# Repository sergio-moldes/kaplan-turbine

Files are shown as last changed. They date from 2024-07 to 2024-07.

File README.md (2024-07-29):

# Kaplan Turbine Design

## Project Description

This project involves the design and analysis of a Kaplan-type turbine, which includes the sizing and analysis of the necessary parameters for the design of the runner, distributor, draft tube, and spiral casing. A CAD design has been created, and CFD simulations have been carried out to verify the performance of the design.

## Technologies Used

- **3D Modeling**: SolidWorks
- **Technical Documentation**: AutoCAD

## Repository Contents

- `/cad_models`: Contains CAD files in .stl, .step, .iges formats.
- `/documentation`: Technical drawings and project documentation in PDF format.

## Installation and Usage

To view and modify the CAD models:

1. Clone the repository: `git clone https://github.com/sergio-moldes/turbina-kaplan.git`
2. Open the files in SolidWorks or your preferred software.

## Contributions

Contributions are welcome. Please open an issue or submit a pull request to discuss any changes you wish to make.

## License

This project is licensed under the MIT License - see the [LICENSE](LICENSE) file for details.

## Project Documentation

The project has been thoroughly documented in the following PDF file: [Kaplan Turbine Design Documentation](documentation/Memoria_turbina_kaplan_final.pdf)

### Documentation Summary

#### 1. Introduction

Describes the project objective and provides an overview of the Kaplan turbine design.

#### 2. Nomenclature and Symbols

List of symbols and nomenclature used in the design calculations.

#### 3. Runner Calculations

Detailed calculations for the sizing of the runner, including initial parameters, outer diameter, free passage section, and hydraulic performance.

#### 4. Distributor Design

Calculations and design of the distributor blades, incidence angle, and blade height.

#### 5. Draft Tube Calculations

Cavitation analysis and suction height, sizing of the draft tube.

#### 6. Spiral Casing Design

Sizing and design of the spiral casing that directs the flow to the runner.

#### 7. CAD Design

CAD design process of the runner, distributor, draft tube, and spiral casing, including chord and angle correction.

### Project Images

Here are some images of the final CAD design:

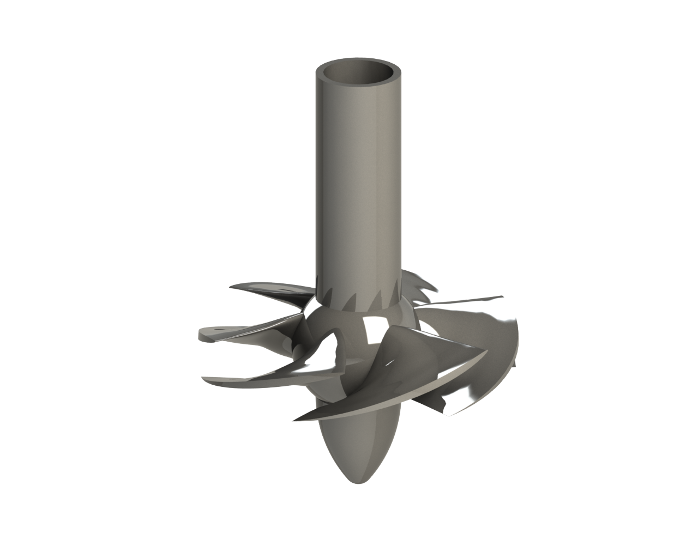
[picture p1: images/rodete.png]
Runner

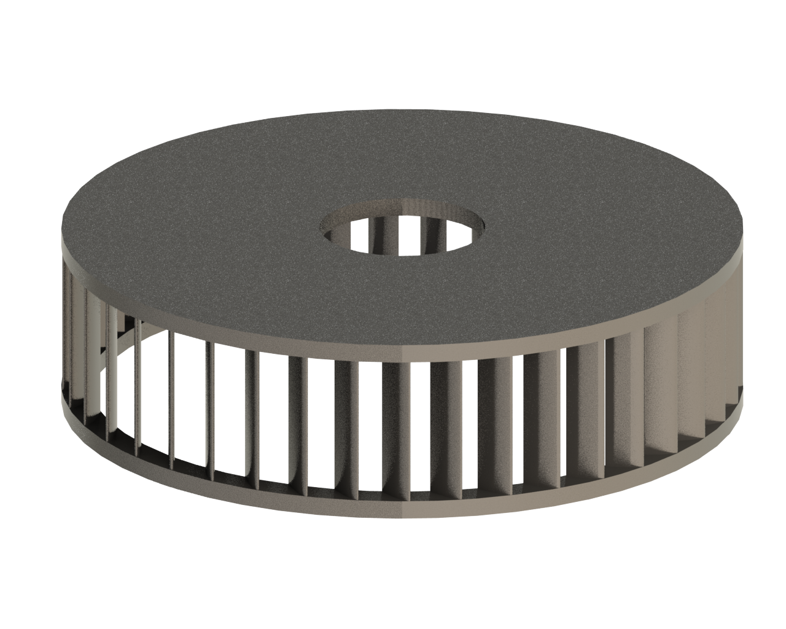
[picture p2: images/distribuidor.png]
Distributor

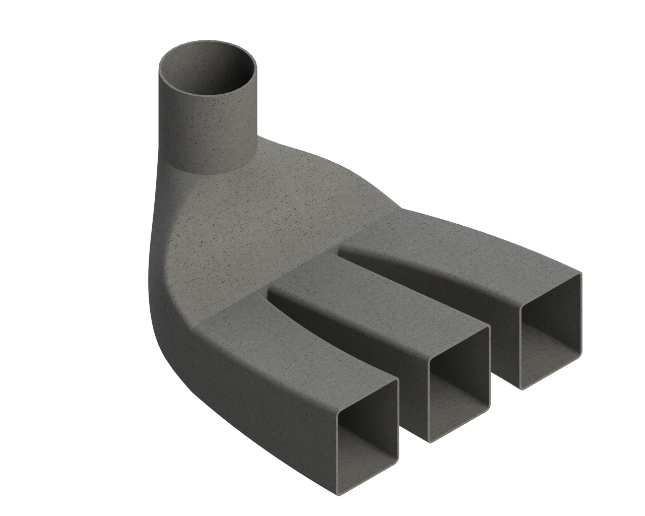
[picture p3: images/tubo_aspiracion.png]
Draft Tube

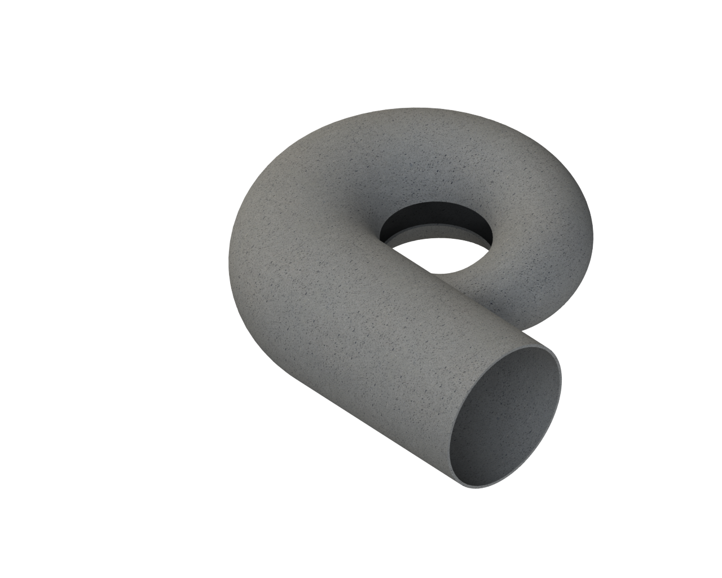
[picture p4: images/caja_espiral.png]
Spiral Casing


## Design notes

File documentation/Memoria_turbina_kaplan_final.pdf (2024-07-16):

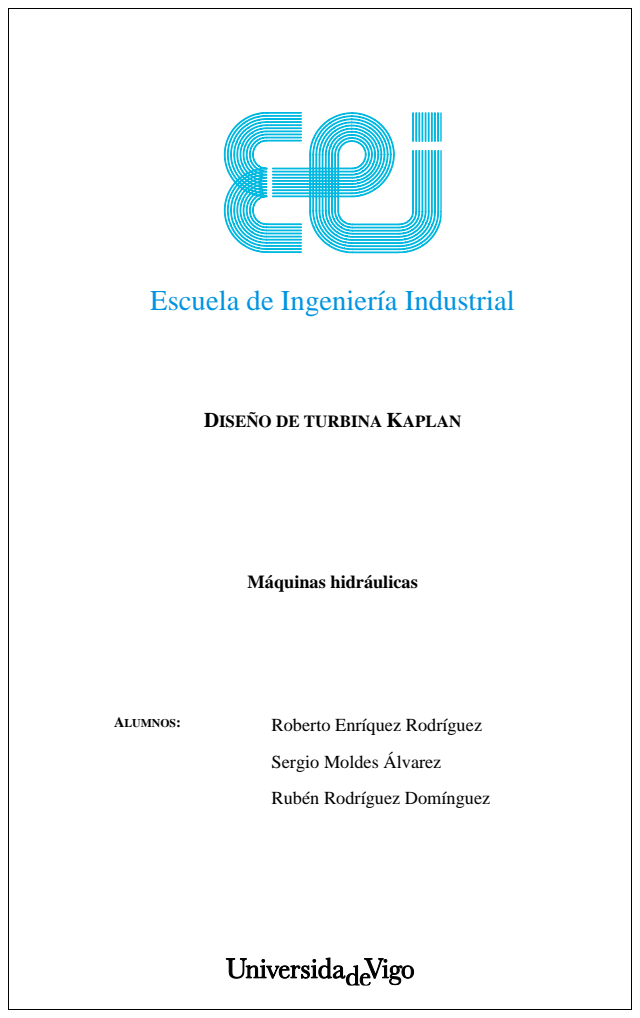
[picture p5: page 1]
Máquinas hidráulicas; ALUMNOS:; Roberto Enríquez Rodríguez

Escuela de Ingeniería Industrial

DISEÑO DE TURBINA KAPLAN

Sergio Moldes Álvarez

Rubén Rodríguez Domínguez

DISEÑO DE TURBINA KAPLAN¡ERROR! NO SE ENCUENTRA EL ORIGEN DE LA REFERENCIA.

CONTENIDO

ÍNDICE DE TABLAS

ÍNDICE DE FIGURAS

### 1 INTRODUCCIÓN

En este documento se realiza el diseño previo al diseño fino de una turbina tipo Kaplan. Estas, son turbinas axiales, donde el flujo es paralelo al eje de rotación, y de reacción pura, donde el fluido cambia de presión a medida que se desplaza a través de la turbina, cediendo su energía. Emplean energía cinética y de presión para mover el rodete, donde antes de llegar el agua al rodete, parte de la energía de presión que trae el agua en su caída se transforma en energía cinética en el distribuidor.

El agua a la salida del rodete se dirige al tubo de aspiración, generándose una depresión, con el fin de aumentar la energía hidráulica absorbida por el rodete. Este tubo desemboca en el canal de desagüe, devolviendo el agua al cauce.

Este tipo de turbina opera con alturas pequeñas y caudales grandes, siendo clasificada como rápidas, teniendo un valor de velocidad específica superior a 300.

El punto de operación estudiado en este documento es de:

H = 36,2 (m) Q = 280 (

m³

s

)

Para ello se realiza el dimensionamiento y análisis de los parámetros necesarios para el diseño del rodete, distribuidor, caja espiral y tubo de aspiración, con el fin de cumplir el punto de operación mencionado anteriormente. Para ello se realizarán los cálculos, sus correspondientes comprobaciones, la elección del perfil a emplear en los álabes y posteriormente el diseño en CAD.

### 2 NOMENCLATURA Y SIMBOLOGÍA

RODETE
SÍMBOLO | NOMBRE | UNIDADES
ns | Velocidad específica | rpm
Q | Caudal | m³ /s
H | Altura de diseño de la turbina | m
N | Potencia útil | CV − MW
n | Velocidad de rotación | rpm
p | Pares de polos | -
f | Frecuencia | Hz
η | Rendimiento total | %
D1 | Diámetro exterior | m
d1 | Diámetro interior | m
Q11 | Engullimiento | m³ /s
u | Velocidad periférica o de arrastre | m/s
u1 | Velocidad periférica o de arrastre a la entrada del rodete | m/s
u2 | Velocidad periférica o de arrastre a la salida del rodete | m/s
g | Gravedad | m/s 2
S | Sección libre de paso | m²
ηH | Rendimiento hidráulico | %
Vm | Velocidad meridional | m/s
V1 | Velocidad absoluta a la entrada del rodete | m/s
V2 | Velocidad absoluta a la salida del rodete | m/s
Vu1 | Componente periférica de la velocidad absoluta a la entrada del rodete | m/s
Vu2 | Componente periférica de la velocidad absoluta a la salida del rodete | m/s
β1 | Ángulo de los álabes a la entrada del rodete | Grados
β2 | Ángulo de los álabes a la salida del rodete | Grados
β∞ | Ángulo de los álabes suponiendo álabes infinitos | Grados
W1 | Velocidad relativa a la entrada del rodete | m/s
W2 | Velocidad relativa a la salida del rodete | m/s
W∞ | Velocidad relativa suponiendo álabes infinitos | m/s
λ | Constante para el cálculo de la cuerda | -
l | Cuerda del perfil | m

t | Paso entre álabes | m
Cl | Coeficiente de sustentación | -
F | Fuerza soportada por las palas | N
P | Presión teórica | Pa
S | Superficie del álabe | m²

DISTRIBUIDOR
SÍMBOLO | NOMBRE | UNIDADES
Vm0 | Componente meridiana radial de la velocidad absoluta de salida | m/s
KVm0 | Factor multiplicativo de la componente meridiana radial | -
g | Gravedad | 2 m/s
H | Altura de diseño de la turbina | m
r | Radio externo del rotor | m
Vu1 | Componente periférica de la velocidad absoluta a la entrada del rodete para el radio externo del rotor | m/s
C | Constante | -
D0 | Diámetro máximo del rodete sobredimensionado | m
D1 | Diámetro máximo del rodete | m
Vu0 | Componente periférica de la velocidad absoluta en el distribuidor | m/s
V0 | Velocidad absoluta en el distribuidor | m/s
B0 | Altura de las directrices | m
α0 | Ángulo de incidencia | Grados

TUBO DE ASPIRACIÓN

SÍMBOLO | NOMBRE | UNIDADES
σ | Coeficiente de Thoma | -
ns | Velocidad específica | rpm
Hs | Altura de succión | m
Hb | Valor de la presión atmosférica local | m
H | Altura de diseño de la turbina | m
ℎv | Tensión del vapor de agua | m. c. a
D3 | Diámetro de entrada del tubo de aspiración | m
A | Altura del tubo hasta el rodete | m
L’ | Longitud entre eje de la turbina y salida del tubo, con ángulo | m

CAJA ESPIRAL
SÍMBOLO | NOMBRE | UNIDADES

Ve | Velocidad de entrada en la caja | m/s
g | Gravedad | 2 m/s
H | Altura de diseño | m
Correspondencia | Factor de caudal correspondiente a la sección estudiada | -
Q | Caudal de diseño | m³ /s
D | Diámetro de la sección de la caja espiral | m

### 3 DIAGRAMA DE FLUJO

### 4 CÁLCULOS DEL RODETE

### 4.1 Parámetros de inicio

Conocido el punto de operación, mencionado anteriormente, siendo una altura de H = 36,2 metros y un caudal de Q = 280 m³/s, inicialmente se busca obtener el valor de la velocidad específica (ns) a partir de la siguiente fórmula:

ns =

n ∗ √N
H ∗ √H

4

[4.1.1]

Para su cálculo se necesita el valor de la velocidad de rotación (n) y el valor de la potencia útil (N), los cuales se obtienen iterando.

Primero, para la obtención del valor de la potencia útil (N), se prefija un valor de rendimiento total, a través de la siguiente fórmula:

N =

1000 ∗ η ∗ Q ∗ H
75

[4.1.2]

Como primer valor se escoge un rendimiento total de η = 90 %, para el cual se obtiene una potencia de N = 121632 CV. Observando este valor, el rendimiento total podría encontrarse entre el 93-94 % según la siguiente tabla extraída de la guía, debido a que el valor de la potencia es superior a 50000 CV.

Tabla 1. Rendimiento frente a potencia.

Teniendo esto en cuenta, se recalculará el valor de la potencia con un rendimiento del 94 %, obteniéndose un valor de N = 127038 CV.
Para el cálculo de la velocidad de rotación (n) se prefija el valor de la velocidad específica empleada en la guía siendo de ns = 457 rpm y el valor de N calculado anteriormente, despejando:

n =

ns ∗ H

5/4
√N

[4.1.3]

Se obtiene un valor de n = 113,85 rpm, correspondiendo para dicha velocidad un par de polos de 26’35, que aproximando al valor entero resulta de 26. Se recalcula el valor de n para 26 pares de polos (p), siendo de 115,39 rpm. Esto es calculado a partir de la siguiente expresión y sabiendo que la frecuencia de trabajo es de f = 50 Hz:

p =

60 ∗ f
n

[4.1.4]

Ya obtenido los valores de la velocidad de rotación (n) y la potencia útil (N), a partir de la fórmula X, se obtiene un valor de ns = 463,158 rpm, próximo al valor prefijado de 457 rpm.

No obstante, se busca un valor de la velocidad específica incluso más próximo para el cual se emplea un η = 91,5 %, obteniendo ns = 456,957 rpm ≈ 457 rpm.

A modo de resumen, los valores obtenidos durante las iteraciones son:

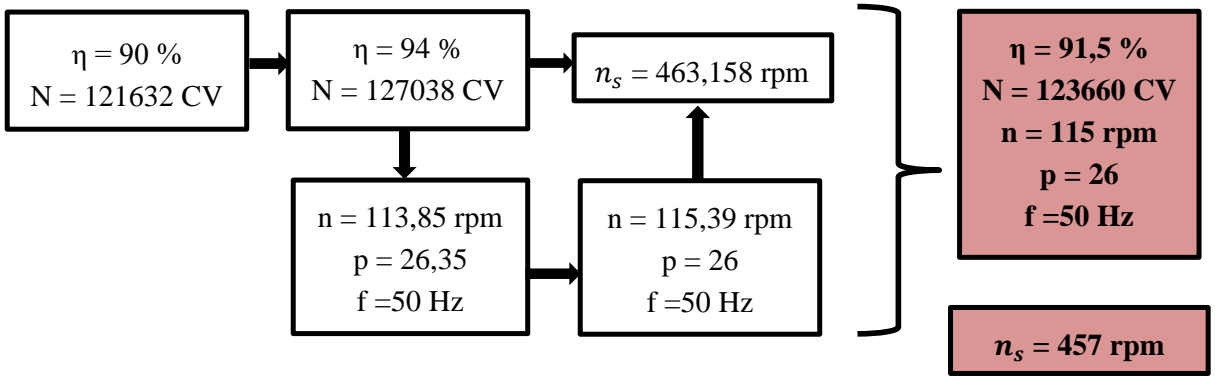
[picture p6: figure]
n = 113,85 rpm; n = 115,39 rpm; ns = 463,158 rpm; n = 115 rpm; ns = 457 rpm

Tras un proceso iterativo de comprobación de los resultados obtenidos en el los cálculos posteriores con respecto a los intervalos de valores correctos para el tipo de turbina a dimensionar, se decide emplear los siguientes parámetros para un mejor ajuste:

Los valores finales obtenidos, son destacados en color verde, siendo los parámetros de inicio que definen la turbina Kaplan (normal) en cuestión, obteniendo una potencia útil, expresada en megavatios de 94,23 MW.

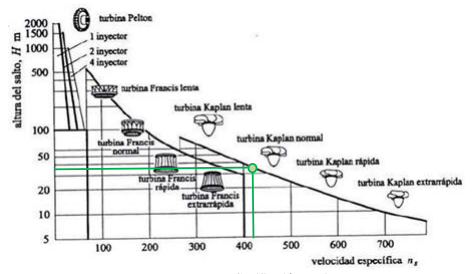
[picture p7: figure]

Figura 1. Clasificación turbinas.

η = 93,5 %
N = 126363 CV
n = 107 rpm
p = 28
f =50 Hz

ns = 429 rpm

### 4.2. Dimensionado del rodete

### 4.2.1. Diámetro exterior

Para la obtención del valor del diámetro externo del rodete, se valoran las 3 opciones expuestas por la guía siendo las siguientes:
- En primera instancia, se puede resolver a partir de la obtención de 2 diámetros, siendo los extremos del intervalo donde se encontrará el valor del diámetro, empleándose la siguiente fórmula:
D1 (m) = 4,8 a 5,5 ∗ √
Q
n

3
= (6, 615 ∼ 7, 579) m | [4.2.1]
- Otra opción planteada es su obtención a través del valor de engullimiento Q11, el cual es atribuido a la descarga consumida por una turbina semejante con valores unitarios de diámetro y altura.
A partir de la siguiente tabla y el valor de la velocidad específica ns = 457 rpm, se interpola para conseguir el valor del engullimiento.

Tabla 2. Engullimiento Q11.

Se obtiene un valor de Q11 = 1′356, con el cual ya se puede obtener el valor del diámetro, con la siguiente fórmula:

D1 = √
Q
Q11 ∗ √H

= √
280
1′356 ∗ √36′2
= 5, 857 m | [4.2.2]
- Como tercera posibilidad, el valor del diámetro (D1), se puede obtener a partir de u1s ,
conocida la velocidad específica, se accede a la siguiente tabla:

Tabla 3. U1s frente ns.

Interpolando se obtiene un valor de u1s = 1, 358, donde despejando el diámetro de la siguiente formula podemos obtener un resultado de:

u1s =

u1
√2 ∗ g ∗ H

=

π ∗ D1 ∗ n
60 ∗ √2 ∗ g ∗ ℎ

D1 =

u1s ∗ 60 ∗ √2 ∗ g ∗ ℎ
π ∗ n

= 7,680 m

[4.2.3]

A continuación, se resumen los valores de D1 obtenidos por los 3 métodos, donde finalmente se tomará como valor único y de referencia, la media de dichos resultados obtenidos:

Valores D1 (m)

D1(4,8) | 6,615
D1 (5,5) | 7,579
D1 (Q11) | 5,857
D1 (u1s) | 7,680
D1 (promedio) | 7,097

Tabla 4. Resumen valores D1.

### 4.2.2. Diámetro del cubo central

El diámetro del cubo central corresponde al diámetro interior, donde para su cálculo se realizará siguiendo 2 caminos con la finalidad de encontrar los mejores resultados. La guía propone realizar una aproximación, escogiendo un valor de entre el 40-50 % del diámetro exterior, no obstante, se considera realizar también una interpolación a través de la tabla 2 de este proyecto, siendo en función de la velocidad específica.

Inicialmente, se procede al cálculo del diámetro interior a través de la interpolación y la tabla mencionada, siendo el siguiente intervalo:

ns | d1/D1
400 | 0,450
429 | 0,444
500 | 0,430

Tabla 5. Cálculo d1.

Se obtiene que:

d1
D1

= 0

′444 → d1 = 3, 15 m | [4.2.4]

### 4.2.3. Sección libre de paso

Una vez determinados los valores del diámetro interior (d1) y exterior (D1) del rodete, se calcula la sección que atraviesa el fluido en su paso por él, obteniéndose un valor de:

S =

(D1

2 − d1

2
) ∗ π
4
= 31, 77 m2 | [4.2.5]

### 4.2.4. Rendimiento hidráulico

El rendimiento hidráulico, ηH, tiene en cuenta las pérdidas mecánicas y las pérdidas secundarias asociadas a fugas de agua, rozamiento, ventilación, etc. Este rendimiento se puede considerar, en términos generales, entre un 3-8 % superior al rendimiento total, por lo que, conocido el rendimiento total η = 93,5 %, se considera el valor más desfavorable del intervalo dado por la guía (3 %), resultando:

ηH = η + 3 % = 93,5 % + 3 % = 96, 5 % | [4.2.6]

### 4.3. Diagrama de velocidades

Para el cálculo y diseño de los álabes, se tomará uno como base que se dividirá en 9 cortes, para las cuales se obtendrán sus correspondientes valores de ángulos y velocidades, calculados por analogía con las siguientes expresiones.

### 4.3.1. Velocidad meridional

La velocidad meridional es la misma en cualquier sección considerada del rodete, la cual, conocido el caudal (Q) y la sección de paso (S), se obtiene de la siguiente ecuación:

Vm1 = Vm2 = Vm | [4.3.1]

Vm =

Q
S

[4.3.2]

### 4.3.2. Velocidad periférica

En cuanto a la velocidad periférica (u), se realizará el cálculo para cada sección del álabe considerada, empleando la siguiente fórmula:

u =

π ∗ Dsección
60 | ∗ n | [4.3.3]

### 4.3.3. Componente periférica de la velocidad absoluta

Se plantea la ecuación de Euler para su obtención:

ηH ∗ g ∗ H = u1 ∗ Vu1 − u2 ∗ Vu2
| | [4.3.4]

Teniendo en cuenta el tipo de turbina a calcular, axial, se conoce que u es la misma en la entrada y la salida debido a que la sección es la misma:

u1 = u2 = u

Además, la salida del fluido será meridional, por lo que: Vu2 = 0

Por lo que, teniendo en cuenta lo mencionado, se aplica la siguiente fórmula a cada sección estudiada:

Vu1 =

ηH ∗ g ∗ H
u
| | [4.3.5]

### 4.3.4. Ángulos β

Se definen los ángulos de entrada y salida de los álabes del rodete:

Entrada→ β1 = arctg (

Vm
u−Vu1
) | [4.3.6]

Salida → β2 = arctg (

Vm
u
) | [4.3.7]

Considerándose álabes infinitos → β∞ = arctg (
Vm
u−

Vu1
2
) | [4.3.8]

### 4.3.5. Velocidad relativa

W∞ = √(u −
Vu
2

)

2
+ Vm
2 | [4.3.9]

### 4.3.6. Ángulo de ataque

El ángulo de ataque, αi
, se define como el ángulo que forma la cuerda del perfil con la dirección del fluido incidente.
Su determinación se procede a partir del software XFLR5, buscando aquel que se adapte correctamente al coeficiente de sustentación en cuestión. Esto se explicará con más detalle y se mostrarán los valores obtenidos en el apartado 5.2 de este proyecto.

### 4.3.7. Ángulo del perfil

Para el diseño de los álabes se introduce βp, el cual se define como la diferencia entre:

βp = β∞ − αi | [4.3.10]

### 4.3.8. Triángulo de velocidades

A continuación, se muestran los valores de β∞ obtenidos:

| 1 | 2 | 3 | 4 | 5 | 6 | 7 | 8 | 9
β∞ º | 48,00 | 36,27 | 29,20 | 24,51 | 21,20 | 18,72 | 16,79 | 15,24 | 13,96

Tabla 6. Resumen de β∞ calculados.

Para la turbina en cuestión, se considera un intervalo correcto para β∞ de entre 15º y 65º, no siendo estrictamente necesario poseer estos valores o estar dentro del intervalo. Como se observa en los resultados obtenidos, el intervalo en el que se encuentran los cálculos realizados es de aproximadamente entre 14º y 48º, el cual se podría considerar apto. No obstante, se buscarán unos valores más próximos al primer intervalo mencionado, por lo que, tras un proceso iterativo, se decide proceder a realizar el cálculo de d1/D1, en el apartado 4.2.2 de este proyecto, a través de uno de los procedimientos descritos en dicho apartado, en el cual la guía propone coger un valor para el diámetro interior de entre el 40-50 % del diámetro exterior, escogiéndose el siguiente:

d1
D1

= 0

′418 (41,8 %) → d1 = 2, 80 m

A continuación, se expresan los valores finales obtenidos:

| 1 | 2 | 3 | 4 | 5 | 6 | 7 | 8 | 9
Diámetro | 2,80 | 3,29 | 3,78 | 4,26 | 4,75 | 5,24 | 5,73 | 6,21 | 6,70
Vm | 9,62 | 9,62 | 9,62 | 9,62 | 9,62 | 9,62 | 9,62 | 9,62 | 9,62
u | 15,69 | 18,41 | 21,14 | 23,88 | 26,61 | 29,34 | 32,07 | 34,80 | 37,53
Vu1 | 21,85 | 18,61 | 16,21 | 14,35 | 12,87 | 11,68 | 10,68 | 9,84 | 9,13
Vu2 | 0,00 | 0,00 | 0,00 | 0,00 | 0,00 | 0,00 | 0,00 | 0,00 | 0,00
β1 º | -57,38 | -88,81 | 62,87 | 45,28 | 35,00 | 28,58 | 24,22 | 21,08 | 18,72
β2 º | 31,52 | 27,59 | 24,47 | 21,95 | 19,88 | 18,16 | 16,70 | 15,46 | 14,38
β∞ º | 63,66 | 46,58 | 36,43 | 29,94 | 25,50 | 22,27 | 19,80 | 17,85 | 16,27
W1 | 11,42 | 9,62 | 10,81 | 13,54 | 16,77 | 20,11 | 23,45 | 26,75 | 29,99
W2 | 10,05 | 16,87 | 21,59 | 25,01 | 27,93 | 30,68 | 33,36 | 36,03 | 38,70
W∞ | 10,74 | 13,25 | 16,20 | 19,28 | 22,35 | 25,39 | 28,41 | 31,39 | 34,34
V1 | 23,87 | 20,95 | 18,85 | 17,28 | 16,07 | 15,13 | 14,38 | 13,76 | 13,26
V2 | 9,62 | 9,62 | 9,62 | 9,62 | 9,62 | 9,62 | 9,62 | 9,62 | 9,62
V∞ | 16,75 | 15,29 | 14,24 | 13,45 | 12,85 | 12,38 | 12,00 | 11,69 | 11,44
Wu1 | -6,16 | -0,20 | 4,93 | 9,53 | 13,74 | 17,66 | 21,39 | 24,96 | 28,40
Wu2 | 15,69 | 18,41 | 21,14 | 23,88 | 26,61 | 29,34 | 32,07 | 34,80 | 37,53
Tabla 7. Resumen de los parámetros calculados corregido.

A través de este cálculo, se obtiene un intervalo aproximado de β∞ de entre 16-64º, siendo más próximo al intervalo de diseño de 15-65º, por lo que se decide emplear los valores obtenidos con este procedimiento.

El triángulo de velocidades para el corte medio (5), resulta de la siguiente manera:

Figura 2. Triángulo de velocidades.

### 4.4. Dimensionado de los álabes

### 4.4.1. Número de álabes

Para la determinación del número de álabes (Z) que tendrá la turbina, se proponen 2 caminos para su cálculo.

- A partir de la tabla 2 y conocido el valor de ns (429 rpm), se obtiene que el número de palas tiene que ser:

Z = 5 ∼ 6 álabes

- Otro método sería su obtención a partir de la siguiente tabla:

Tabla 8. Cálculos del numero de palas.

Como se cuenta con una altura de H = 36’2 metros corresponderían 8 álabes, pero como está próximo a 35 metros, se consideran Z= 6 álabes ya que también se encontraría dentro del intervalo del anterior método.

### 4.4.2. Paso entre los álabes

Conocido el número de álabes (Z) y el diámetro externo e interno, el paso entre álabes resulta:

t =

π ∗ (

D1 + d1
2

)

Z

[4.4.1]

### 4.4.3. Cuerda de los álabes

El valor de la cuerda del álabe se obtiene a partir del paso entre álabes y un factor multiplicativo que depende de la velocidad específica ns
(429 rpm):

λ =

78

ns

2/3= 1′371 | l = λ ∗ t | [4.4.2]

Aplicando las anteriores expresiones del paso y la cuerda de los álabes, se obtiene para cada punto de estudio los resultados mostrados en la siguiente tabla:

| 1 | 2 | 3 | 4 | 5 | 6 | 7 | 8 | 9
t | 1,466 | 1,721 | 1,977 | 2,232 | 2,487 | 2,742 | 2,998 | 3,253 | 3,508
l | 2,010 | 2,360 | 2,710 | 3,060 | 3,410 | 3,761 | 4,111 | 4,461 | 4,811
l ⁄ t | 1,371 | 1,371 | 1,371 | 1,371 | 1,371 | 1,371 | 1,371 | 1,371 | 1,371
t ⁄ l | 0,729 | 0,729 | 0,729 | 0,729 | 0,729 | 0,729 | 0,729 | 0,729 | 0,729

Tabla 9. Cálculo de la cuerda y el paso del álabe.

Debido a que el cociente entre la cuerda y el paso presenta el mismo valor para los 9 puntos, se obtiene una turbina con los bordes de los álabes totalmente rectos, es decir, una turbina de diseño tradicional.

### 4.4.4. Fuerza y coeficiente de sustentación

En este apartado se calcula la fuerza y el coeficiente de sustentación, valores de gran importancia a la hora de diseñar y escoger los alabes más adecuados para el funcionamiento objetivo.
Para el cálculo del coeficiente de sustentación se necesita conocer la fuerza soportada por cada pala, la superficie sobre la que se aplicará la fuerza y la velocidad relativa media suponiendo alabes infinitos

Cl =

2 ∗ F
ρ ∗ W∞(m)

2
∗ S

[4.4.3]

W∞(m) corresponde a la velocidad media obtenida en las superficies anteriores que viene dada por la siguiente expresión:

W∞(m) =

W∞(n) + W∞(n+1)
2

[4.4.4]

El cálculo de la fuerza total soportada por las palas “F” viene dada por la siguiente expresión:

F =

S ∗ P
Z

[4.4.5]

La presión se obtiene mediante la siguiente expresión:

P = ρ ∗ g ∗ H ∗ ηH

[4.4.6]

Para el cálculo de la superficie se realiza una aproximación lineal, suponiendo los radios como líneas rectas y dividiendo cada tramo en un rectángulo y dos triángulos (Figura 3 izquierda). Para comprobar si se comete algún error por usar dicha aproximación, se realiza un CAD en el cual se utilizan los valores reales, usando los radios y calculando la cuerda para cada uno, creando así la superficie real de cada tramo (Figura 3 derecha). Este cálculo de la cuerda corregida se utilizará posteriormente para el diseño del CAD, descrito en el punto 9. Una vez hecho esto se puede ver que la aproximación es buena, arrojando los mismos valores hasta el 8 decimal.

S1 | 0,53269093 | →
S2 | 0,61800898 | →

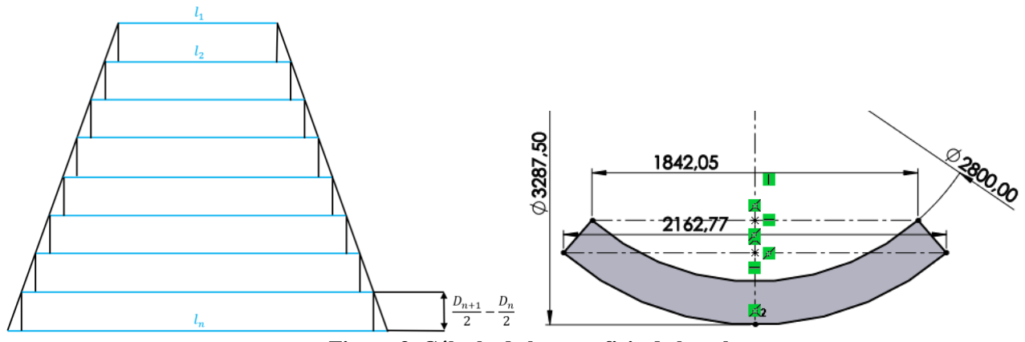
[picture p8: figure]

Figura 3. Cálculo de la superficie de la pala

Se obtienen 8 superficies correspondientes a los 9 cortes realizados, calculados mediante la siguiente expresión:

S = ln ∗ (

Dn+1
2

−

Dn
2

) +

(ln+1 − ln) ∗ (

Dn+1
2

−

Dn
2

)

2

[4.4.7]

Una vez se tienen estas superficies se realiza una curva de ponderación para repartir la fuerza que soportará cada una de estas, siendo esta una estimación
Además, se considera una ponderación de la fuerza que se aplica a lo largo de la pala, de tal manera que se consiga un empuje mayor en la zona del 60/70% del radio, debido a que será la zona más eficiente. Los pesos de la ponderación se escogen de manera arbitraria de tal forma que no haya picos bruscos y se obtenga una curva suavizada, la curva de ponderación es la siguiente.

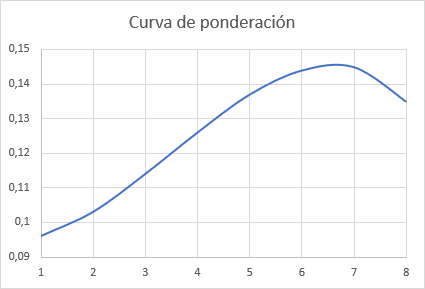
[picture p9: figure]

Figura 4. Curva de ponderación de fuerzas.

| 1 | 2 | 3 | 4 | 5 | 6 | 7 | 8 | 9 | TOTAL
W∞ | 10,74 | 13,25 | 16,20 | 19,28 | 22,35 | 25,39 | 28,41 | 31,39 | 34,34 | -
W∞(m) | 11,992 | 14,724 | 17,740 | 20,815 | 23,873 | 26,901 | 29,900 | 32,866 | - | -
Pt | - | - | - | - | - | - | - | - | - | 342692,73
D ⁄ 2 | 1,4 | 1,64375 | 1,8875 | 2,13125 | 2,375 | 2,61875 | 2,8625 | 3,10625 | 3,35 | -
l | 2,010 | 2,360 | 2,710 | 3,060 | 3,410 | 3,761 | 4,111 | 4,461 | 4,811 | -

S | 0,533 | 0,618 | 0,703 | 0,789 | 0,874 | 0,959 | 1,045 | 1,130 | - | -
Pond | 0,096 | 0,103 | 0,114 | 0,126 | 0,137 | 0,144 | 0,145 | 0,135 | - | -
F | 36464,88 | 39123,78 | 43302,05 | 47860,16 | 52038,42 | 54697,32 | 55077,16 | 51278,74 | - | 379842,503
Cl | 0,952017 | 0,583988 | 0,391276 | 0,280136 | 0,208956 | 0,157581 | 0,117953 | 0,084030 | -

Tabla 10. Resumen de los parámetros para el diseño del alabe.

Después de los cálculos de los esfuerzos del álabe, se calcula su espesor, asumiendo que este tendrá un valor igual a un porcentaje de la cuerda de la primera sección, siendo este porcentaje, un 25% en la raíz y un 10% en la punta.

| 1 | 2 | 3 | 4 | 5 | 6 | 7 | 8 | 9
e | - | 0,5901 | 0,5395 | 0,4889 | 0,4384 | 0,3878 | 0,3370 | 0,2866 | 0,2360
e l | - | 0,2500 | 0,1991 | 0,1598 | 0,1285 | 0,1031 | 0,0820 | 0,0642 | 0,0490
% | - | 0,2500 | 0,2286 | 0,2071 | 0,1847 | 0,1643 | 0,1429 | 0,1214 | 0,1000

Tabla 11.Cálculo del porcentaje de espesor del alabe.

### 5 ELECCIÓN DE LOS PERFILES

### 5.1 Introducción

En este apartado se procede a realizar un estudio aerodinámico de varios perfiles para el diseño de los álabes, con el objetivo de escoger el álabe que mejor se adecue al diseño de la turbina de estudio. Se utiliza el software XFLR5, que es una herramienta de análisis de perfiles de álabe operando a bajos números de Reynolds.
Los perfiles que se van a usar, son con código NACA de cuatro dígitos, se explica a continuación el significado de cada uno de los dígitos:
- 1º Digito: Da el camber máximo en porcentaje de cuerda.
- 2º Digito: Representa la localización del camber máximo en la décima de cuerda.
- 3º y 4º Dígito: otorgan el máximo espesor en porcentaje de la cuerda.
A continuación, se muestra una imagen detallando las diferentes partes de un perfil alar.

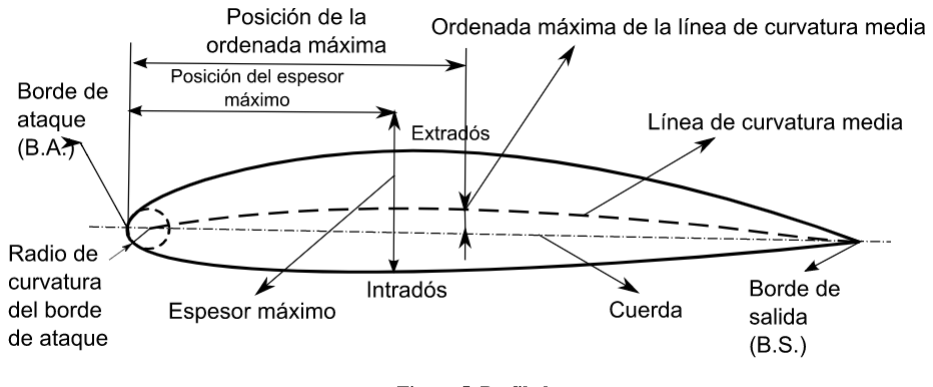
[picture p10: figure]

Figura 5. Perfil alar.

### 5.2 Procedimiento de elección del perfil

El procedimiento a seguir para la adecuada elección del perfil del álabe es el siguiente. En una primera instancia, con el máximo valor del espesor en porcentaje de la cuerda de cada sección ya se sabe los dos últimos dígitos del perfil NACA, posteriormente se analiza en el software los diferentes perfiles candidatos que se consideran más eficientes. Para llevar a cabo tal evaluación, con el valor del coeficiente de sustentación Cl previamente calculado para cada sección, se obtiene el ángulo de ataque de cada perfil que se ajuste lo máximo al Cl. Además, con la gráfica Cl-Cd se comparan los diferentes perfiles, buscando que, para el Cl exigido, el perfil tenga el menor coeficiente de arrastre, consiguiendo así el punto de máxima eficiencia aerodinámica.
Una vez determinados los perfiles con el ángulo de ataque deseado, se analiza la gráfica del coeficiente de presión, con el fin de garantizar que el valor máximo de esta no supere el coeficiente de cavitación calculado previamente. También hay que tener en cuenta que se busca la mayor área entre las curvas.
El coeficiente de cavitación nombrado anteriormente se calcula de la siguiente manera:

Ca =

P − Pv
1
2

∗ ρ ∗ V2

2

= 2, 14 | [5.2.1]

A continuación, se explica paso a paso el procedimiento para la elección del perfil en una de las secciones, el perfil a estudiar es un perfil NACA XX10 (coeficiente de sustentación exigido:

0,217), particularmente se lleva a estudio los siguientes perfiles: NACA 1610, NACA 1710, NACA 2610, NACA 2710.

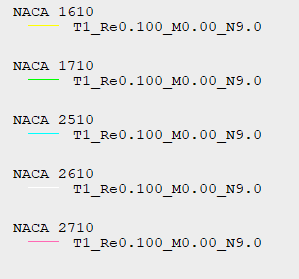
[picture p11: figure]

Figura 6. Perfiles NACA XX10.

### 5.2.1 Comportamiento Cl-Cd

Partiendo de un coeficiente de sustentación de 0,217, se observa el comportamiento de los coeficientes de arrastre de cada perfil en la gráfica Cl-Cd, buscando el perfil con el coeficiente de un menor valor, siendo estos los perfiles NACA 1610, NACA 1710 y NACA 2510. Sin embargo, no hay una gran diferencia de coeficiente de arrastre entre uno y otros perfiles, por lo que se siguen teniendo en cuenta los cinco iniciales.

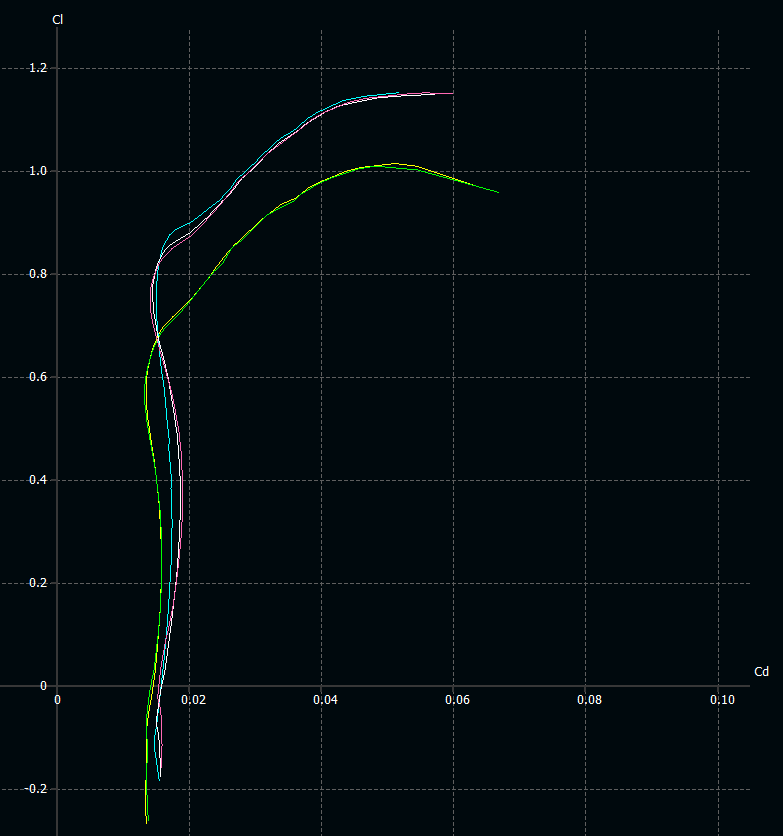
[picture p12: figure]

Figura 7. Gráfica Cl-Cd.

### 5.2.2 Angulo de ataque

Con la gráfica Cl-alfa proporcionada por el software, se estima el ángulo de ataque de cada perfil para el coeficiente de sustentación exigido, el inconveniente es que no se obtiene una gran precisión al obtener estos ángulos de una gráfica como tal. Para arreglar esto, hay que irse a la gráfica de presiones del perfil e ir probando diferentes ángulos de ataque, próximos al obtenido gracias a la gráfica Cl-alfa, hasta que el Cl sea igual o muy similar al exigido. En la siguiente tabla se muestran los ángulos de ataque para cada perfil.

PERFIL | ANGULO DE ATAQUE
NACA 1610 | 1,377º
NACA 1710 | 1,545º
NACA 2510 | 0,59º
NACA 2610 | 0,952º
NACA 2710 | 1,265º
Tabla 12. Cálculo del ángulo de ataque.

Figura 8.Gráfica Cl-Alpha

### 5.2.3 Resultados

Finalmente, con los ángulos de ataque escogidos, se comparan los perfiles basándose en la gráfica del coeficiente de presiones, estas gráficas se muestran a continuación.

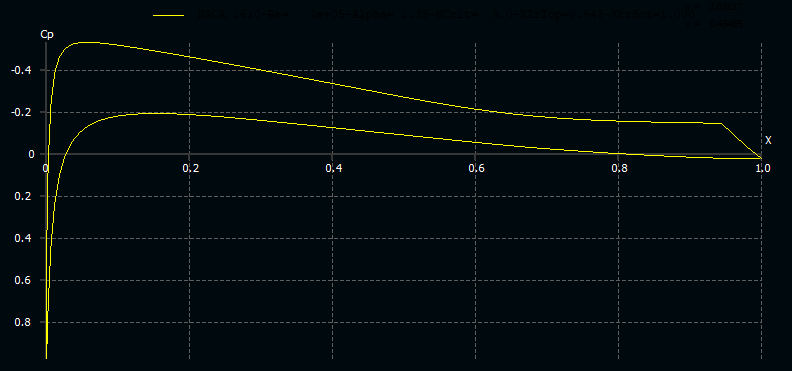
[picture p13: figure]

Figura 9. Gráfica Cp para NACA 1610.

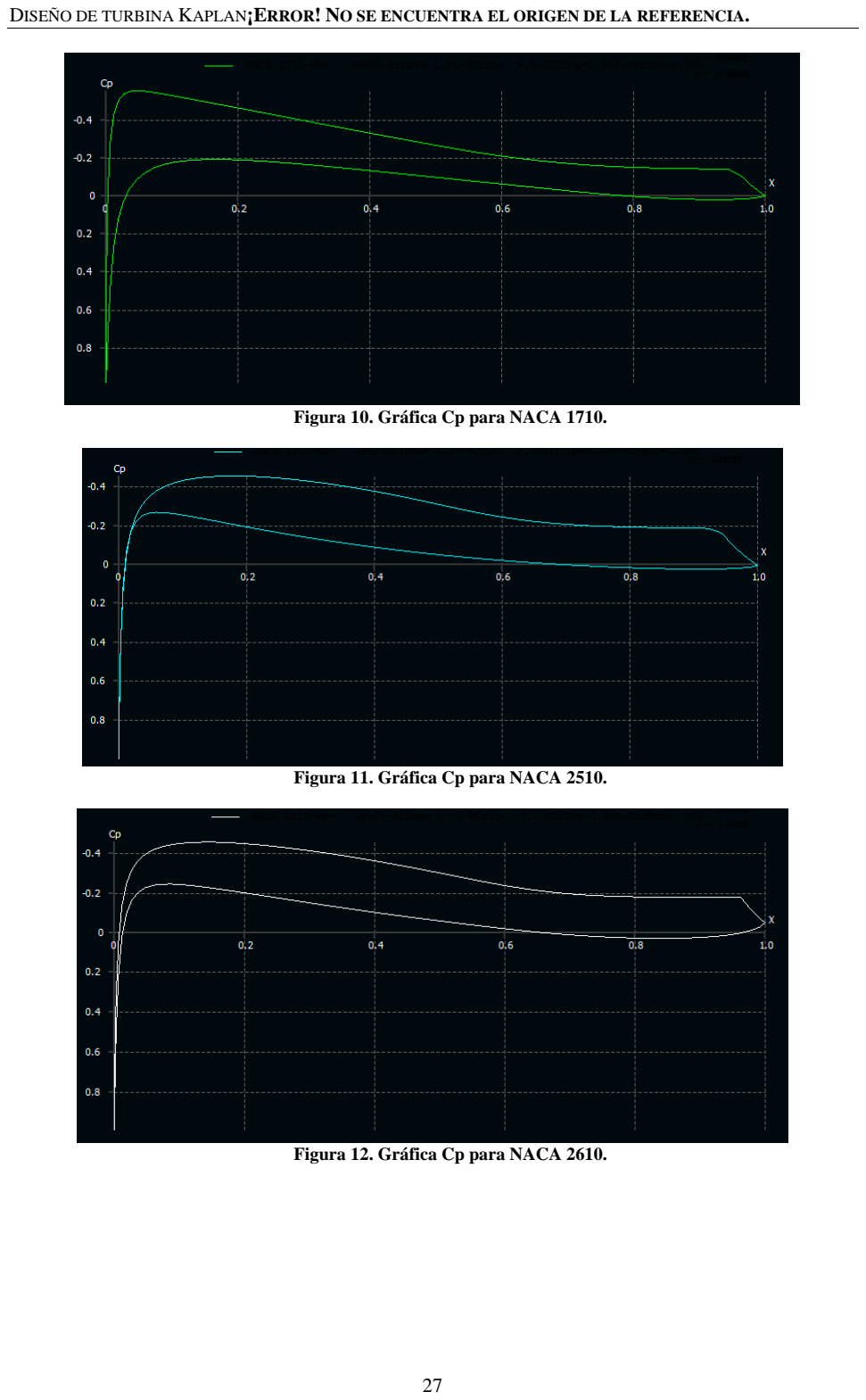
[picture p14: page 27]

Figura 10. Gráfica Cp para NACA 1710.

Figura 11. Gráfica Cp para NACA 2510.

Figura 12. Gráfica Cp para NACA 2610.

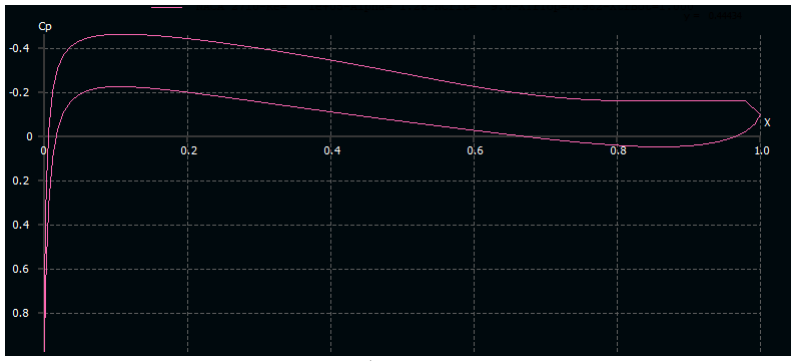
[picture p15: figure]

Figura 13. Gráfica Cp para NACA 2710.

Se puede observar que, para cualquiera de las gráficas de presión obtenidas, el coeficiente de presión no sobrepasa al coeficiente de cavitación calculado. A pesar de que los perfiles NACA 1610, NACA 1710 y NACA 2510 son más eficientes aerodinámicamente, como ya se ha comentado, se descartan por los siguientes motivos, los perfiles NACA 1610 y NACA 1710 presentan un ligero pico a la entrada, mientras que el NACA 2510, al hacer zoom en la gráfica, se observa que las líneas se cruzan en la entrada. Para los perfiles restantes, las gráficas son muy similares, tanto la gráfica de presiones, como la de Cl-Cd, optándose finalmente con el perfil NACA 2610 debido a la tendencia que llevan los ángulos de ataque para las otras secciones. Análogamente, se realizan los mismos pasos para cada una de las secciones, se muestra en la siguiente tabla, un resumen de los diferentes perfiles y sus características.

PERFILES | COEFICIENTE DE SUSTENTACIÓN | ANGULO DE ATAQUE
NACA 6725 | 0,9865 | 7,33º
NACA 4720 | 0,6051 | 2,952º
NACA 4716 | 0,4054 | 1,329º
NACA 2612 | 0,2903 | 1,141º
NACA 2610 | 0,2165 | 0,952º
NACA 2608 | 0,1644 | 0,775º
NACA 1606 | 0,1213 | 0,671º
NACA 1004 | 0,0870 | 0,105º
Tabla 13. Resumen cálculo de perfiles.

### 6 CÁLCULOS DEL DISTRIBUIDOR

### 6.1 Introducción

El distribuidor es un elemento constituido por álabes fijos, que tiene como finalidad dirigir el fluido hacia el rodete, regulando el caudal admitido, teniendo así la capacidad de modificar la potencia de la turbina para su ajuste a las variaciones de carga de la red eléctrica.

Los álabes del distribuidor se ubican a una distancia considerable de los álabes del rodete, entre los cuales debe existir una sincronización entre sus ángulos, debido a que los álabes del rodete varían su ángulo de inclinación para adecuarse al caudal.

En el distribuidor, la energía de presión disminuye y la de velocidad aumenta, para que posteriormente en el rodete, la presión siga disminuyendo, transformando esta energía de presión y cinética en energía útil en el eje.

↓ Presión ~ ↑ Velocidad ⟹ ↓ Energia potencial de presión ~ ↑ Energía cinética

Además, éste orienta la velocidad absoluta del fluido en la región de vórtices libres, donde cada partícula se mueve en una trayectoria circular a una velocidad que varía, la cual se encuentra previamente a la entrada al rodete, consiguiendo así que el fluido alcance los álabes con el ángulo de ataque analizado en el apartado 4.1.3 de este documento.

### 6.2 Cálculo de los álabes del distribuidor

Inicialmente se busca calcular la componente meridional:

Vmo = kvmo ∗ √2 ∗ g ∗ H | [6.2.1]

Previamente a su cálculo se necesita kvmo, valor que depende de la velocidad específica y el cual a través de interpolación y la siguiente tabla resulta de: kvmo = 0,284.

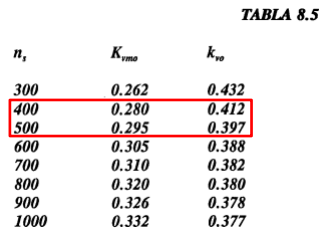
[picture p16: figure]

Tabla 14. Cálculo de kvmo y kvo.

Durante el proceso del cálculo se comprueba que la ecuación de vórtice libre es válida desde la salida del distribuidor hasta la entrada del rodete, siendo la siguiente:

r ∗ Vu = constante = C | [6.2.2]

El valor de dicha constante se puede calcular estableciendo como punto de estudio la entrada de un álabe del rodete, donde r1 y Vu1 son conocidos:

r1 ∗ Vu1 = C | [6.2.3]

Obtenido C, se procede al cálculo de Vuo, para el cual se necesita previamente el valor de Do, donde para su cálculo se estima que es 1,1 veces el valor del diámetro máximo del rodete, siendo:

Do = 1,1 ∗ D1

[6.2.4]

Entonces:

Vuo =

C
Do
2

[6.2.5]

Para el cálculo de Vo se necesita previamente el valor de kvo, donde análogamente al procedimiento seguido para kvmo, resulta de kvo = 0,407.

Vo = kvo ∗ √2 ∗ g ∗ H | [6.2.6]

Obtenido los valores de Vmo y Vo, se calcula el valor del ángulo de incidencia ∝o, siendo este el formado por la dirección de Vuo (tangente a la circunferencia de radio ro) y la bisectriz de ángulo formado por las caras en la punta del álabe.

tan ∝o=

vmo

vuo

[6.2.7]

Finalmente, obtenidos los valores anteriores, se calcula el valor de la altura de dichos álabes Bo:

Vmo =

Q
π ∗ Do ∗ Bo

→ Bo =

Q
π ∗ Do ∗ Vmo

[6.2.8]

Los valores obtenidos en los cálculos anteriores se encuentran tabulados a continuación:

VARIABLE | RESULTADO
Vmo | 7,578
C | 30,586
Do | 7,37
Vo | 10,864
∝o | 42,396
Bo | 1,596

Tabla 15. Resumen cálculos.

Figura 14. Palas directrices del distribuidor.

### 4.4.5. Número de álabes

El número de álabes se obtiene en función del diámetro de la circunferencia que pasa por el punto de salida de los álabes, Do, siendo un total de Z = 40,37 ~ 41 álabes.

Tabla 16. Cálculo del número de álabes.

### 7 CÁLCULOS DEL TUBO DE ASPIRACIÓN

### 7.1 Introducción

Para el diseño del tubo de aspiración, se tiene en cuenta dos parámetros para su correcto funcionamiento, la cavitación y la altura de aspiración. A continuación, se procede al cálculo de dicha altura, donde previamente se debe determinar el valor del coeficiente de Thoma, validando que la turbina no presenta cavitación.
Esta cavitación es un proceso que se produce cuando la presión absoluta del fluido baja hasta igualar el valor de la presión de vapor, a causa de una velocidad elevada, provocándose un proceso de vaporización. Pasado a vapor, el fluido libera gases formándose burbujas que prosiguen el camino y que, ganando presión de nuevo, estas explotan generando problemas de ruido, daño en los componentes y pérdidas de rendimiento.

### 7.2 Coeficiente de cavitación de Thoma

Para estudiar la cavitación se obtiene el valor del coeficiente de cavitación de Thoma de forma empírica, a partir de la siguiente expresión, el cual depende de la velocidad especifica:

σ = 0,0000154 ∗ ns

1,7 → σ = 0,4599 | [7.2.1]

Conocido el coeficiente de cavitación y ns
, se observa validando gráficamente que la turbina en estudio no presenta cavitación, encontrándose en la zona segura:

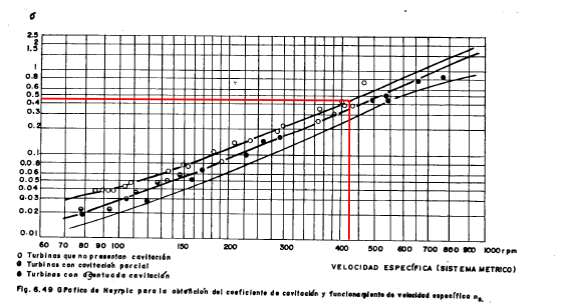
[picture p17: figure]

Figura 15. Gráfico para la obtención del coeficiente de cavitación.

### 7.3 Altura de succión

Una vez calculado el coeficiente de cavitación, se verifica que el valor de éste se ve aumentado a medida que aumenta el valor de la velocidad específica, pudiendo ocurrir un valor negativo para la altura de succión (desnivel entre entrada del tubo y nivel del agua en el canal de fuga), Hs, lo que conlleva a que la entrada del tubo de aspiración debe encontrarse por debajo del nivel del agua, situación que solo es viable con la utilización de un tubo de aspiración curvo.

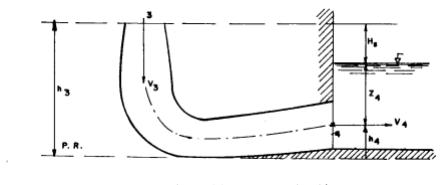
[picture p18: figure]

Figura 16.Tubo de aspiración.

Determinado esto, su cálculo se obtiene a partir de la siguiente expresión:

Hs = Hb − σ ∗ H − ℎv

[7.3.1]

Siendo:
-Hs: Altura de succión.
-Hb: Valor de la presión atmosférica local.
- σ: Coeficiente de Thoma.
-H: Altura de diseño de la turbina.
-hv: Tensión de vapor del agua.

Para Hb se supone una altitud de 0 metros y se escoge su valor medio siendo de:

1 atm → 10,33 mca

Tabla 17. Cálculo de Hb.

Los valores de las variables anteriores se tabulan a continuación:

VARIABLE | RESULTADO
Hb | 10,3287
σ | 0,4599
H | 36,2000
ℎv | 0,2386
Hs | -6,5596

Tabla 18. Cálculo altura de succión

Debido a que el valor de la altura de succión es negativo, se dice que la turbina trabaja a contrapresión.

### 7.4 Dimensionado del tubo de aspiración

Teniendo en cuenta que el diámetro del rodete, D1 = 6,7 m, es coincidente con el diámetro de entrada del tubo de aspiración, D3, para el diseño en CAD del tubo de aspiración, se sigue el siguiente esquema, siendo para turbinas con un diámetro mayor a 2,13 m, siendo éste el caso.

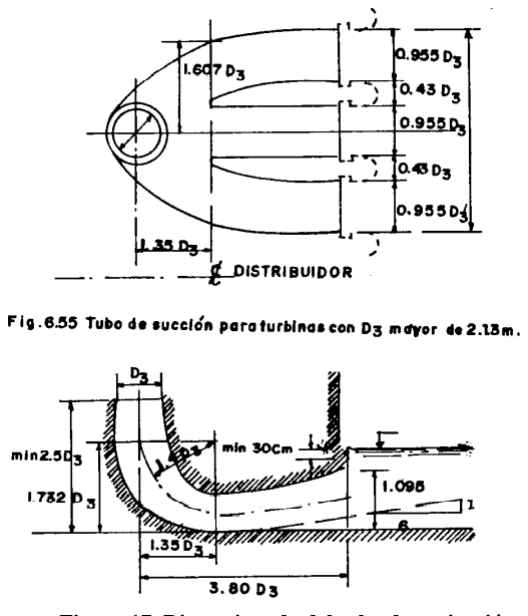
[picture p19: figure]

Figura 17. Dimensionado del tubo de aspiración.

Se dispone de 3 bocas de salida, con un caudal Q/3 por cada una, debiéndose esta división a que, las dimensiones para una única boca de salida serían muy elevadas, pudiendo llegar a fracturarse, facilitando también la obra civil con dicha división.
A partir de la siguiente tabla se podrá determinar con exactitud la altura del tubo hasta el rodete, definiéndose en la anterior imagen como mínimo 2,5 veces D3. Además, se consigue el valor de la longitud L’, el cual corresponde a la distancia entre el eje de la turbina y la salida del tubo difusor, teniendo en cuenta el ángulo de elevación que posee.

Tabla 19. Gráfico A y L’

Se obtienen los siguientes valores:

Longitud (L’) | 25.5 m
Altura del tubo hasta el rodete (A) | 18 m
Tabla 20. Resultados de A y L’

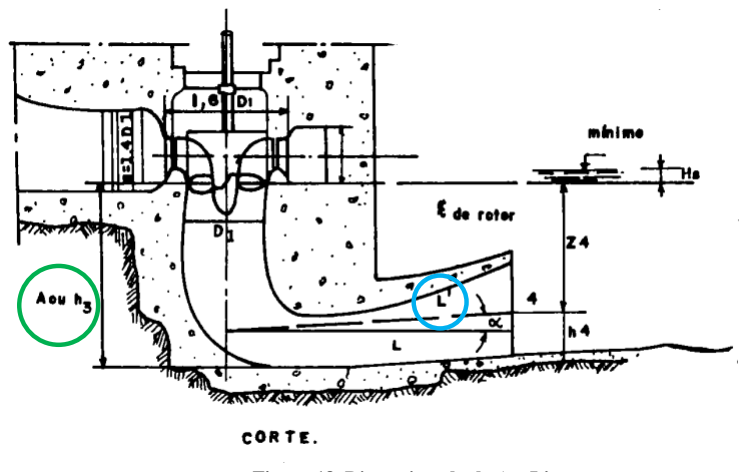
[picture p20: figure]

Figura 18. Dimensionado de A y L’

### 8 CÁLCULOS DE LA CAJA EN ESPIRAL

La caja o cámara en espiral se encarga de recoger el fluido proveniente de la tubería forzada, que, junto con el distribuidor, dirige dicho fluido hacia el rodete.
Esta transforma la energía de presión del fluido en energía cinética, haciendo que en cualquier punto de la cámara esta energía cinética sea igual, consiguiendo que la velocidad tangencial del fluido sea constante en la periferia del rodete.

Para definir la caja espiral se considera una sección transversal circular, donde inicialmente se procede a calcular la velocidad con la cual llega el fluido, siendo la velocidad de entrada (Ve) . Para el cálculo de dicha velocidad, la guía define un factor variable entre 0’12-0’15, el cual se cogerá el valor intermedio (0’135), cuya fórmula corresponde para una construcción en hormigón.

Ve = 0,12 a 0,15 ∗ √2 ∗ g ∗ H → 0,135 ∗ √2 ∗ g ∗ H = 3, 6 m/s | [8.1.1]

Obtenida la velocidad de entrada, se procede a dimensionar la cámara espiral, donde se dividirá en 8 secciones para posteriormente obtener sus diámetros. Para ello se considera una distribución uniforme del caudal a través de la salida hacia el distribuidor, siendo la velocidad de entrada constante en toda la espiral.

D = √
4 ∗ Q ∗ Correspondencia
π ∗ Ve

[8.1.2]

Sección | D | Q | Correspondencia
8 | 3,52 | 35 | 1/8
7 | 4,98 | 70 | 1/4
6 | 6,09 | 105 | 3/8
5 | 7,04 | 140 | 1/2
4 | 7,87 | 175 | 5/8
3 | 8,62 | 210 | 3/4
2 | 9,31 | 245 | 7/8
1=Entrada | 9,95 | 280 | 1

## 9 DISEÑO DE CAD

### 9.1 Rodete

Para el diseño de este componente se utilizan los diámetros en los que se realizan los cortes del alabe y los perfiles NACA correspondientes, mencionados con anteriormente.

El diseño se realiza mediante dos métodos, uno quedando los alabes como una superficie vacía, sin espesor, y la segunda, dejando los álabes como un sólido. Debido a esto se selecciona el segundo método por asemejarse más a algo real.

Para comenzar con el diseño se realiza es una circunferencia sólida de 150mm de espesor, que representa el cubo central, teniendo por diámetro el más pequeño del álabe. A continuación, se realizan 9 semicircunferencias, correspondientes a los cortes realizados para el diseño.

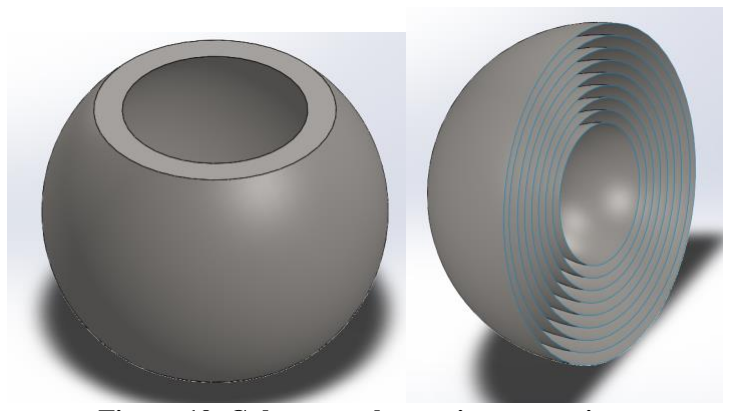
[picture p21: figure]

Figura 19. Cubo central y secciones sucesivas

Las semicircunferencias se realizan para poder obtener el perfil NACA deseado en forma de superficie sin que SolidWorks arroje error alguno al generar la superficie. Para obtener el perfil NACA en SolidWorks se utiliza el comando “curva por puntos XYZ” y se van cargando dichos perfiles mediante los archivos.txt obtenidos en XFLR5. Estas se dimensionan para obtener las medidas calculadas anteriormente, pero al momento del diseño hay que tener en cuenta que la cuerda calculada pertenece a la longitud “L” del perímetro de la circunferencia (“L” en figura 20), y como el perfil se dimensiona en un plano, se le da la medida de la cuerda (“K” en figura 20) de dicho circulo para evitar ese porcentaje de error.

Figura 20. Corrección de cuerda para diseño

K = 2 ∗ sin (

l
D

) ∗ (D
2
⁄ ) | [9.1.1]

| 1 | 2 | 3 | 4 | 5 | 6 | 7 | 8 | 9
l | 2,010 | 2,360 | 2,710 | 3,060 | 3,410 | 3,761 | 4,111 | 4,461 | 4,811
D | 2,800 | 3,288 | 3,775 | 4,263 | 4,750 | 5,238 | 5,725 | 6,213 | 6,700
K | 1,842 | 2,163 | 2,483 | 2,804 | 3,125 | 3,446 | 3,766 | 4,087 | 4,408

Tabla 21. Cálculo de cuerda corregida

Con esto solucionado, se dimensionan mediante los valores obtenidos para K y se giran los perfiles según el ángulo de perfil correspondiente (figura 21 izquierda), tomando como ejemplo el perfil NACA-2610 perteneciente al corte 5. Se proyecta dicho perfil sobre las semicircunferencias mencionadas anteriormente, obteniendo una superficie con la curvatura perteneciente a dicha esfera y eliminando el resto (figura 21 derecha).

Figura 21. Creación de perfil de álabe

| 1 | 2 | 3 | 4 | 5 | 6 | 7 | 8 | 9
β∞ | 63,657 | 46,581 | 36,434 | 29,942 | 25,498 | 22,266 | 19,797 | 17,850 | 16,272
αi | 7,330 | 2,952 | 1,329 | 1,141 | 0,952 | 0,775 | 0,671 | 0,105 | 0,105
βp | 56,327 | 43,629 | 35,105 | 28,801 | 24,546 | 21,491 | 19,126 | 17,745 | 16,167

Tabla 22. Cálculo de beta de perfil

Se repite esta operación para todos los perfiles y se unen utilizando el comando “recubrir sólido” obteniendo un alabe de la turbina.

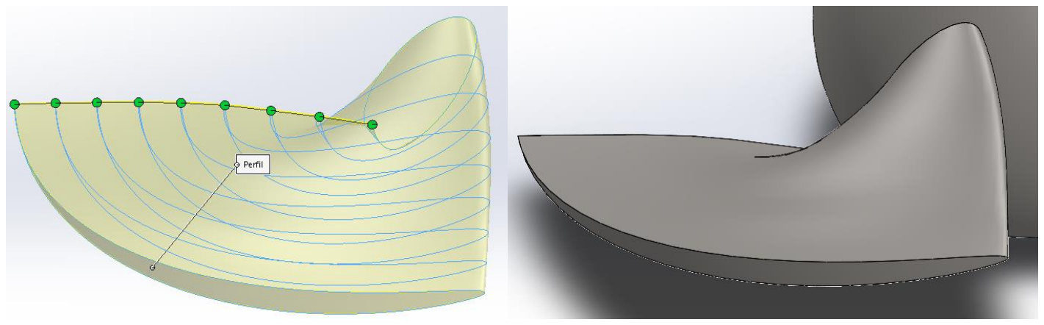
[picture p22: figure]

Figura 22. Creación de álabe de turbina

Para obtener todos los álabes se utiliza el comando “Matriz circular” insertando 5 alabes más para tener un total de 6, que son los calculados para este diseño.

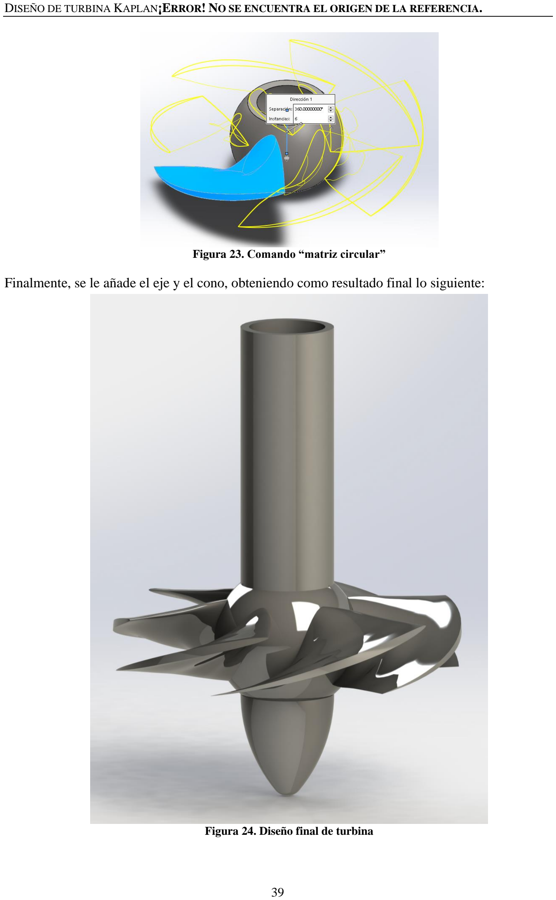
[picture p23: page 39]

Figura 23. Comando “matriz circular”

Finalmente, se le añade el eje y el cono, obteniendo como resultado final lo siguiente:

Figura 24. Diseño final de turbina

### 9.2 Distribuidor

Para el distribuidor el diseño es mucho más simple que para la parte del rotor.
Para la parte inferior se hacen dos circunferencias en un croquis, la interior de diámetro igual a la salida de los álabes y la exterior 1.1 veces este diámetro. Debido al gran tamaño de este se diseña en hormigón, por lo que se le da un espesor de 200mm. Cabe destacar que se realizan taladros, para situar los álabes, y permitir que estos giren en caso de ser necesario, pero no se considera que el diseño de dicho sistema entre de las competencias de este trabajo.
Después se selecciona el perfil NACA correspondiente y se realiza el mismo procedimiento que para el rotor, dándole las dimensiones calculadas en el apartado 6 de este trabajo.
Para la parte superior se le da como diámetro exterior el mismo que la inferior, siendo el diámetro inferior el correspondiente.

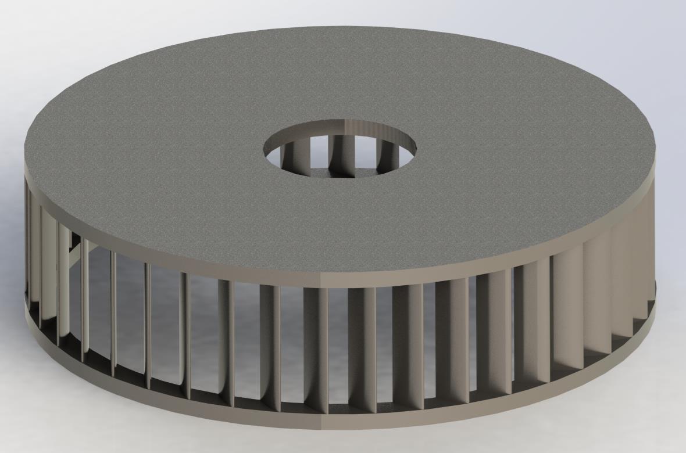
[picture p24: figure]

Figura 25. Diseño final de distribuidor

### 9.3 Tubo de aspiración

Se diseña siguiendo las medidas obtenidas mediante la guía. Debido a que se trata de una superficie compleja, se diseña por superficies, aplicándole posteriormente un espesor de 200mm, debido a que se realiza en hormigón.
Se divide en 5 superficies principales, buscando el mejor diseño posible de esta manera.
La primera será el tramo circular de entrada, creado mediante un barrido de superficie y que tendrá un diámetro interior de 6.7 m, siendo este el diámetro exterior de los alabes de la turbina (Figura 26 izquierda).
El siguiente tramo será la unión entre este tubo y las 3 entradas de caudal. Este diseño es el más complejo ya que se necesitan del uso de varias curvas guía externas en 3 dimensiones, necesitando que estén ajustadas correctamente, ya que de lo contrario SolidWorks no creará un espesor para dicha figura (Figura 26 derecha).

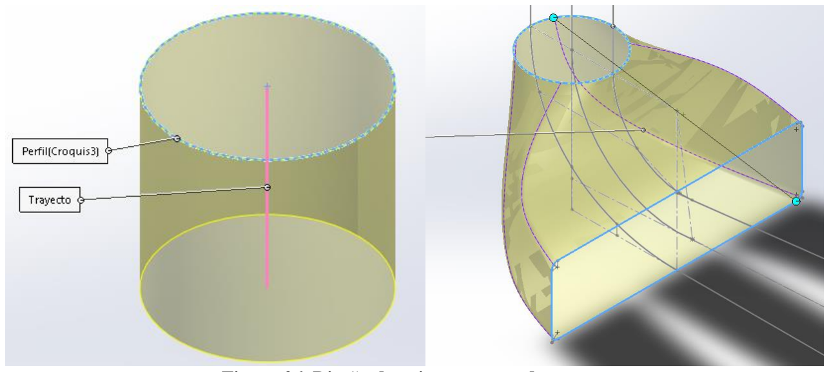
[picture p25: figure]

Figura 26. Diseño de primer y segundo tramo

Las 3 superficies restantes serán las correspondientes a los tubos de aspiración, siendo estos creados por separado y formando la figura final.

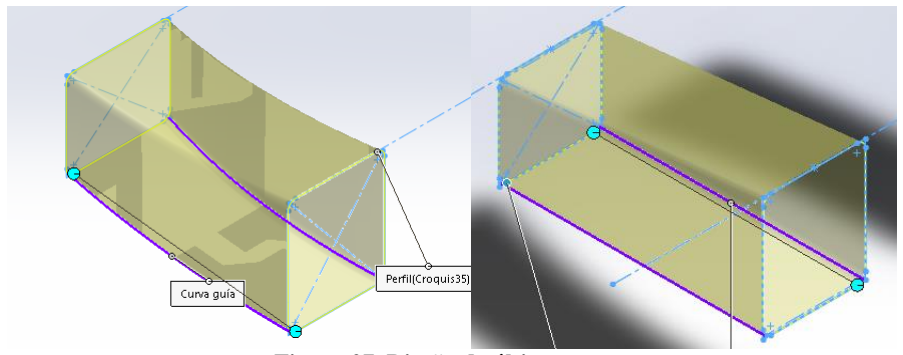
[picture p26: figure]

Figura 27. Diseño de último tramo

Finalmente, se le da el espesor y se rellena el hueco entre los 3 tubos y el segundo tramo.

Figura 28. Diseño final de tubería de aspiración

### 9.4 Cámara espiral

Se diseña en dos tramos, también por superficies, siendo el primero de estos el tramo recto correspondiente a la tubería forjada y el segundo la propia espiral. Para el diseño de la espiral se realizan las circunferencias pertinentes y se realiza un “spline”, a modo de curva guía exterior con las medidas proporcionadas en el punto 8, siendo la curva guía interior el diámetro correspondiente al del diseño del distribuidor.

Figura 29. Diseño primer y segundo tramo

Se recorta el tramo que se encuentra en conflicto con el tramo recto y se le da espesor a dicha superficie, volviendo a eliminar el exceso de material para un ajuste correcto.

Figura 30. Recorte de material sobrante

Por último, se hace un corte en el interior de esta para que el agua fluya a través de él y entre en el distribuidor, teniendo este una anchura igual a la del distribuidor.

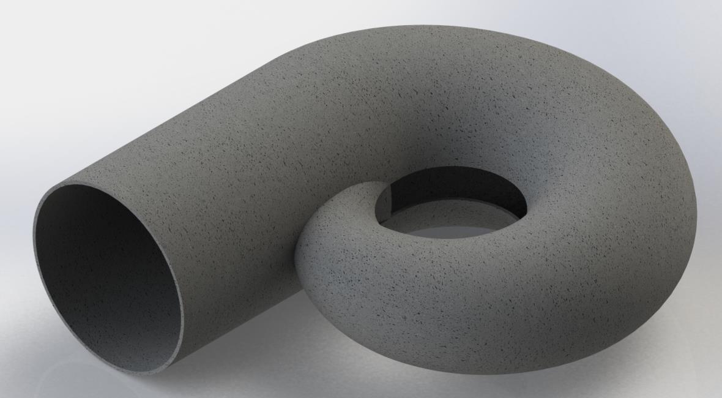
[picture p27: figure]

Figura 31. Diseño final de cámara espiral

### 9.5 Ensamblaje final

A continuación, se muestra el ensamblaje final en su totalidad y una perspectiva seccionada con el detalle de como encajarían todas en la zona de la turbina, ya que no es apreciable desde la vista total.

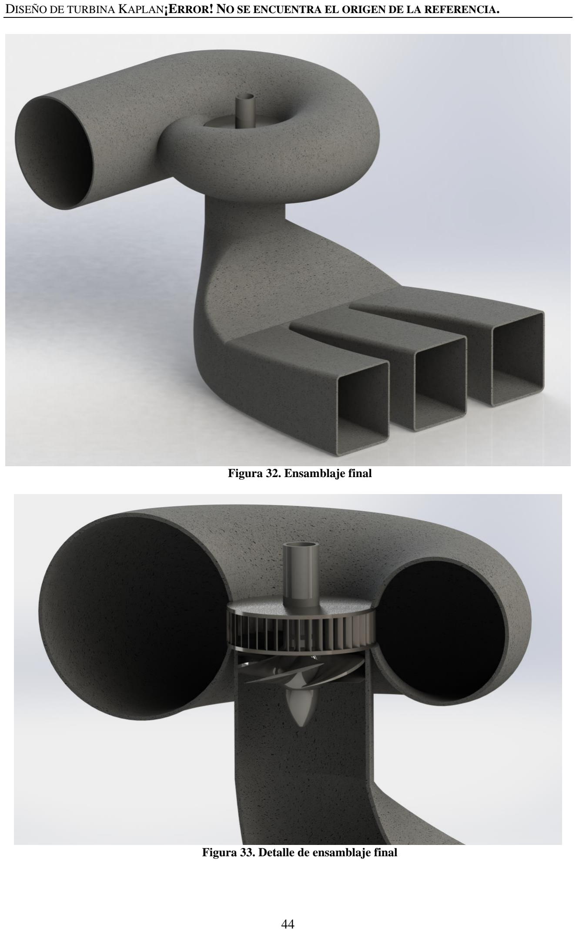
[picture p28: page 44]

Figura 32. Ensamblaje final

Figura 33. Detalle de ensamblaje final

### 10 CONCLUSIONES

En este proyecto se ha llevado a cabo el diseño de una turbina Kaplan a partir de una guía de diseño seleccionada con tal objetivo.
El objetivo, es el diseño de una turbina con el punto de operación de una instalación hidráulica ubicada en Islandia, cuyo nombre es Castrelo, dichos datos de partida son: Q=280 m3/s y H=36.2 m.

La turbina diseñada cuenta con seis palas pese a que lo más normal en estas máquinas axiales es tener 3 palas, pero este desencadena en problemas de equilibrados y ruidos. LA intención del proyecto es obtener una pala equilibrada pese a que no tenga el máximo rendimiento posible. Además, se han tenido que tomar varias decisiones según se iba avanzando con el proyecto, por nombrar alguna, la decisión relativa a los ángulos β, puesto que, en una primera instancia, los valores calculados eran entre 14º y 48 º. Mientras que, teóricamente, los valores ideales serían entre 15º y 65º. Este inconveniente se ha solucionado mediante un proceso iterativo, consiguiendo finalmente que el ángulo β calculado sea entre 16º y 64º aproximadamente, asumiendo estos datos como aceptables para el diseño de estudio.

Finalmente, se puede decir, que se ha diseñado una turbina axial, con todos sus componentes principales, tomando varias decisiones en cuanto los diferentes procedimientos expuestos en la guía y cuestionando todos los resultados obtenidos. Se han escogido sus perfiles alares y diseñado en un software CAD la totalidad de la turbina.

### 11 BIBLIOGRAFÍA

### 11.1 Guía principal

- Álvaro Orozco López, “Guía para el diseño de turbinas hidráulicas”, Corporación universitaria autónoma de occidente, Santiago de Cali, 1995.

### 11.2 Información complementaria

- P. Fernández Diez, “Libros sobre Ingeniería Energética”. Disponible en:
https://pfernandezdiez.es/es/
- F. de Siervo and F. de Leva, “Modern trends in selecting and designing Kaplan turbines”, Water Power & Dam Construction, Part one. December 1977-January 1978.
Disponible en:
https://pdfslide.net/documents/modern-trends-in-selecting-and-designing-kaplan-turbines.html (https://pdfslide.net/documents/modern-trends-in-selecting-and-designing-kaplan-turbines.html)
- J. Agüera Soriano, “Mecánica de Fluidos Incompresibles y Turbomáquinas Hidráulicas”, IV edición, Editoral Ciencia 3 S.L., Córdoba, 1996.
Disponible en:
http://www.uco.es/termodinamica/Libros/MECANICA%20DE%20FLUIDOS%20INCO MPRESIBLES%20Y%20TURBOMAQUINAS%20HIDRAULICAS.%20PROBLEMAS %20RESUELTOS.pdf (http://www.uco.es/termodinamica/Libros/MECANICA%20DE%20FLUIDOS%20INCOMPRESIBLES%20Y%20TURBOMAQUINAS%20HIDRAULICAS.%20PROBLEMAS%20RESUELTOS.pdf)
- Mataix, C.,”Mecánica de Fluidos y Máquinas Hidráulicas”, Editorial del Castillo S.A., 1986.
Disponible en:
https://conver2.files.wordpress.com/2012/11/ingenieria-claudio-mataix-mecanica-de-fluidos-y-maquinas-hidraulicas1.pdf (https://conver2.files.wordpress.com/2012/11/ingenieria-claudio-mataix-mecanica-de-fluidos-y-maquinas-hidraulicas1.pdf)

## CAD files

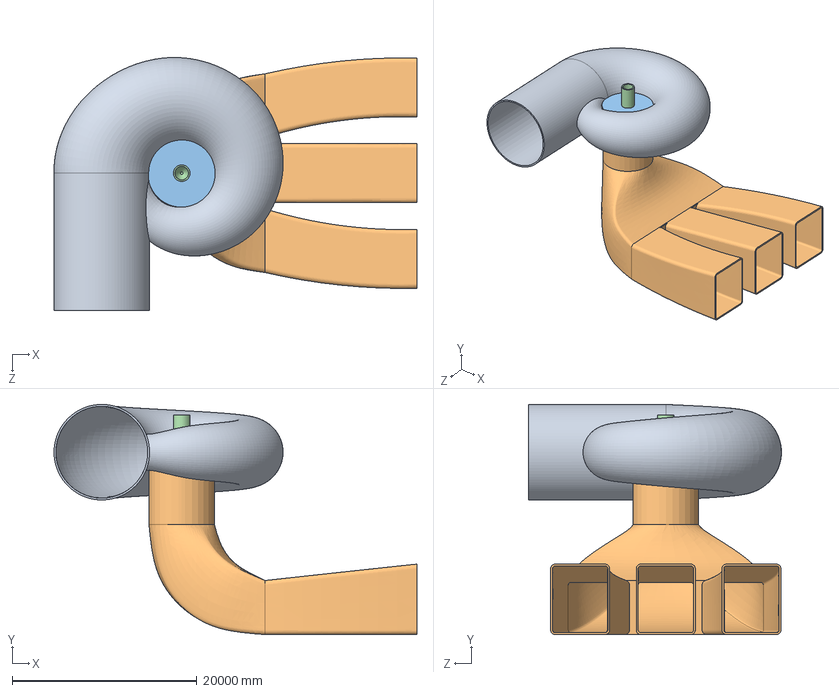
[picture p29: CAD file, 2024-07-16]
cad_models/Ensamblaje.SLDASM
39318.6 x 24931.6 x 27400.7 mm
Caja espiral
Difusor
Distribuidor
Turbina solida

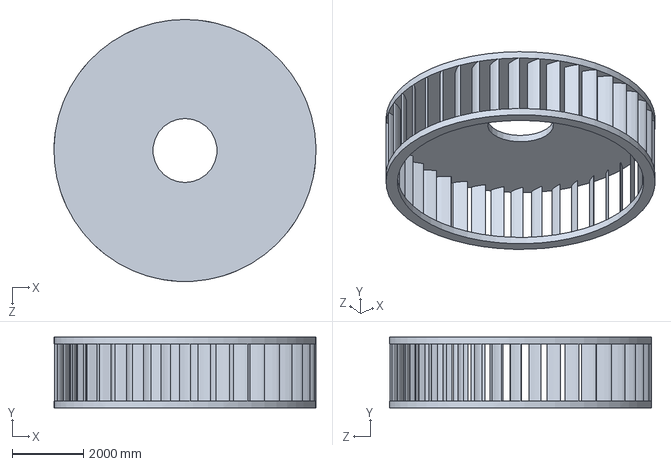
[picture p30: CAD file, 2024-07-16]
cad_models/Distribuidor.SLDPRT
7366.8 x 1996.0 x 7370.0 mm

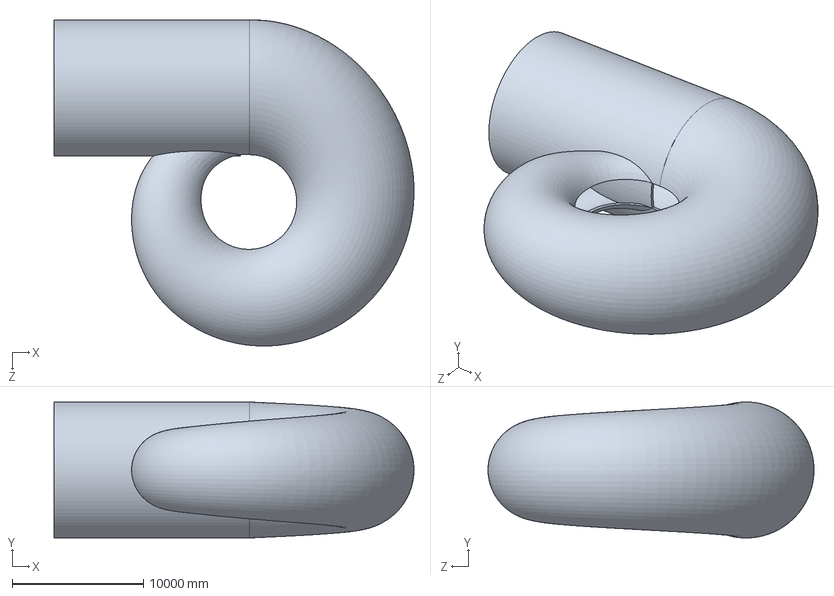
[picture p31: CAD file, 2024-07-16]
cad_models/Caja espiral.SLDPRT
27400.7 x 10350.8 x 24815.0 mm

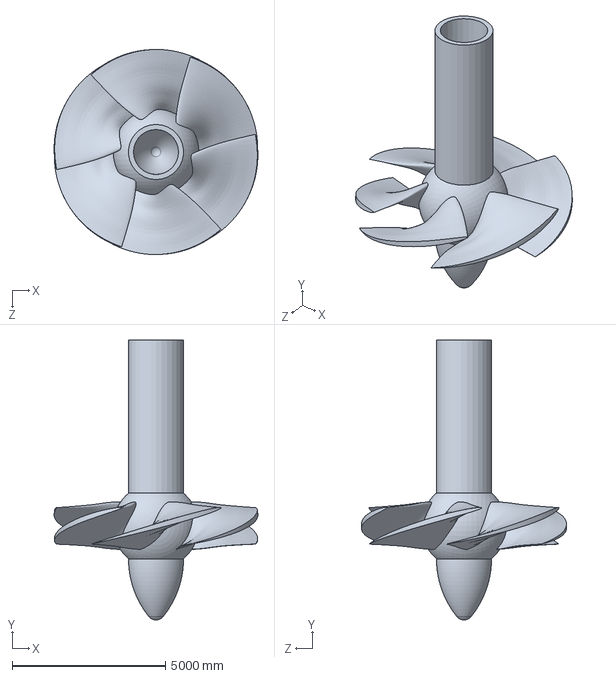
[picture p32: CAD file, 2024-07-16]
cad_models/Turbina solida.SLDPRT
6655.7 x 9144.8 x 6700.0 mm

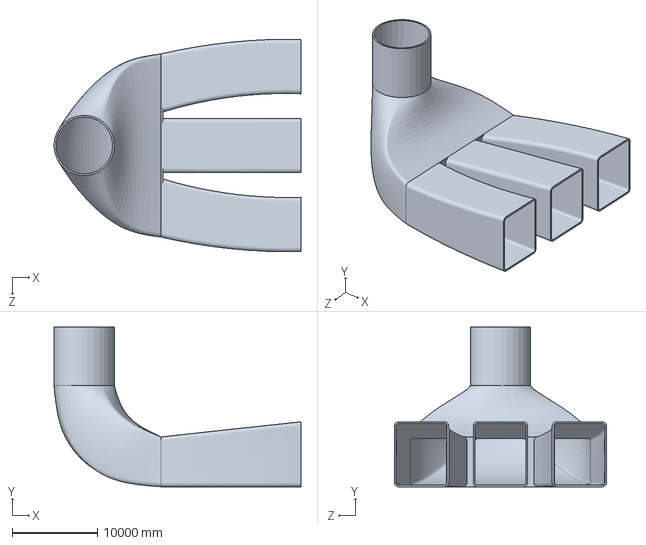
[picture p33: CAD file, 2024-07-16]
cad_models/Difusor.SLDPRT
29032.3 x 18760.0 x 24974.4 mm
